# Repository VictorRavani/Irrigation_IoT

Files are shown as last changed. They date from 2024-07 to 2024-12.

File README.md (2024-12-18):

# Irrigation_IoT

Este projeto abrange o desenvolvimento completo de Hardware e Firmware para controle em IoT. Oferece todas as informações e recursos necessários para que qualquer pessoa possa configurar o sistema de forma independente.



# Atualizações a serem feitas v2: 

- Leds dos optocopadores, como os Leds estão em série acaba não havendo corrente sulficinete para acionalos...
- Conversor USB serial CP2102 pode ser removido pois o ESP32-S3 possui interface USB.
- Troca do conector Micro USB para USB tipo C.
- Desing da PCB adaptadada para um case de mercado.
- Substituir botoões por um encoder rotativo.
- Deixar os demais GPIOS disponíveis para uso utilizando conectores KRE. (Obs.: Prever circuitos de proteção com optoacopladores).

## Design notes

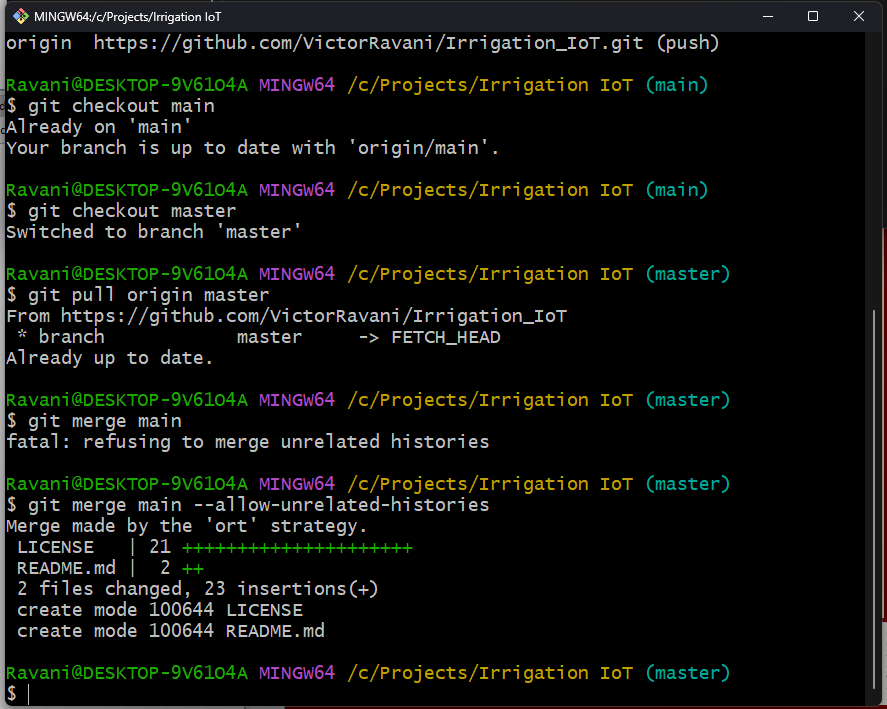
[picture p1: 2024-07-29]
Merge branch master main.png

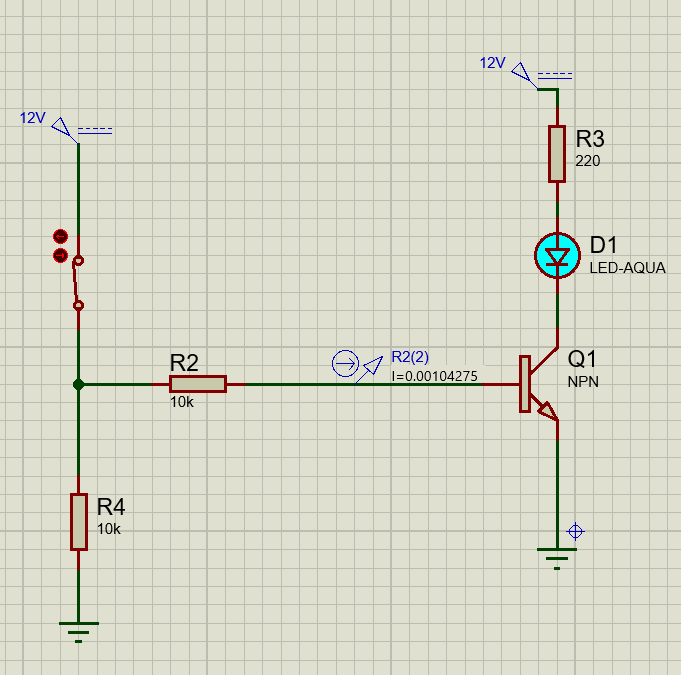
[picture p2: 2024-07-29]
Acionamento Relé.png

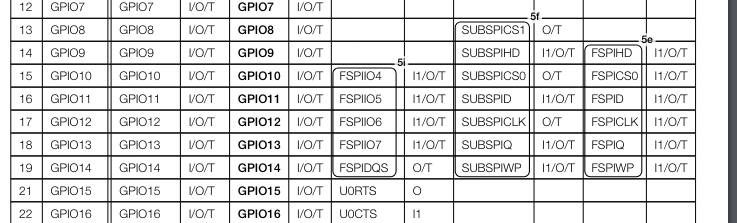
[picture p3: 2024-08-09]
Strappins_ESP32_S3.png

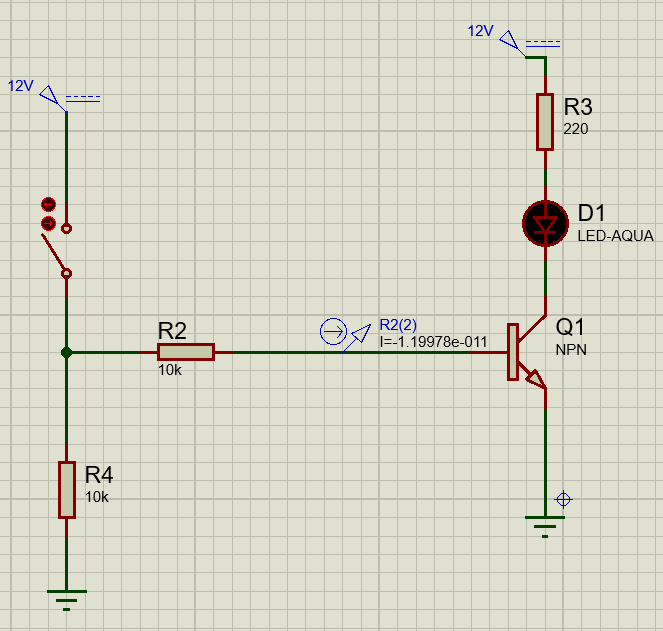
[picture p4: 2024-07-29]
Acionamento Relé aberto.png

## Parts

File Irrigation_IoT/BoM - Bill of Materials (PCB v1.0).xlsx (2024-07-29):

Bill of Materials
Company Name:
Project Name:
Date:
RESISTORS
ID | Qty. | Part Designator | Manufacturer Number | Description
1 |  | R1, R9, R12, R13, R14, R15, R16, R17, |  | Resistor SMD 10K 0805 5%
2 |  | R8, R11 |  | Resistor SMD 2K2 0805 5%
3 |  | R2, R5 |  | Resistor SMD 4K7 0805 5%
4 |  | R3 |  | Resistor SMD 24K 0603 1%
5 |  | R4 |  | Resistor SMD 47K 0603 1%
6 |  | R6, R7, R10 |  | Resistor SMD 220R 0805 5%
CAPACITORS
ID | Qty. | Part Designator | Manufacturer Number | Description
1 | 2 | C1, C7 |  | Capacitor Cerâmico SMD 4,7uF 0805 25V (https://www.eletrodex.net/passivos/capacitores/smd/capacitor-ceramico-smd-0805-x5r-25v)
2 | 9 | C2, C8, C10, C17 |  | Capacitor Cerâmico SMD 10uF 0805 25V (https://www.eletrodex.net/passivos/capacitores/smd/capacitor-ceramico-smd-0805-x5r-25v)
3 | 2 | C3, C5, C6, C9, C11, C12, C13, C14, C15, C16 |  | Capacitor Cerâmico SMD 100nF 0805 50V (https://www.eletrodex.net/passivos/capacitores/smd/capacitor-ceramico-smd-0805-x7r-50v)
INDUCTORS
ID | Qty. | Part Designator | Manufacturer Number | Description
OSCILLATORS
ID | Qty. | Part Designator | Manufacturer Number | Description
TRANSISTORS
ID | Qty. | Part Designator | Manufacturer Number | Description
 |  | Q3, Q4 |  | BC817 NPN (https://www.eletrodex.net/semicondutores/transistores/uso-geral/bc8xxx-transistor-smd)
PROTECTION DEVICES
ID | Qty. | Part Designator | Manufacturer Number | Description
 |  | RV1 (DNP) | MOV-10D431KTR | Varistor 10K AC 275V
DIODES
ID | Qty. | Part Designator | Manufacturer Number | Description
 |  | D1 |  | Diodo Supressor SP0503BAHTG SOT (https://www.acheicomponentes.com.br/circuitos-integrados/kit-5-pecas-diodo-supressor-sp0503bahtg-sot-143-4-smd)
INTREGRATED CIRCUITS
ID | Qty. | Part Designator | Manufacturer Number | Description
 |  | U1, U5 |  | EL817/PC817 ISOLADOR ÓPTICO SMD (https://www.eletrodex.net/semicondutores/opticos/isoladores/el817pc817-isolador-optico)
 |  | IC1 |  | Módulo Esp32-s3 - Esp32-s3-wroom-1 N16r8 (https://produto.mercadolivre.com.br/MLB-3670453135-modulo-esp32-s3-esp32-s3-wroom-1-n16r8-_JM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)
 |  | IC2 |  | Circuito Integrado CP2102-GMR SMD QFN-28 (https://www.acheicomponentes.com.br/circuitos-integrados/smd/circuito-integrado-cp2102-gmr-smd-qfn-28-original-cp2102)
 |  | U1 |  | LM1117DTX-3.3 - 3.3V SMD (https://www.eletrodex.net/semicondutores/ci-s-hibridos/reguladores-lineares/lm1117-regulador-de-tensao-low-dropout)
ELECTROMECHANICS
ID | Qty. | Part Designator | Manufacturer Number | Description
1 | 2 | K3, K4 | MA1RC2 (Metaltex) | Miniature relay AX1RC2 (https://www.eletrodex.net/montagem/reles/miniatura/ma1rc-rele-ultra-miniatura-metaltex)
CONNECTORS
ID | Qty. | Part Designator | Manufacturer Number | Description
1 |  | J1 |  | CONECTOR JACK DC-005 J4, 3T 2,1MM (https://www.eletrodex.net/acessorios/cabos-e-fios/jack/conector-jack-dc-005-j4-3t-2-1mm)
2 |  | J2 |  | CONECTOR USB MICRO-B (https://www.eletrodex.net/conectores/usb/micusb-b5ns-conector-usb-micro-b-para-smd-metaltex)
3 |  | J3, J7 |  | BR7F2-03 (https://www.eletrodex.net/conectores/pci/bornes/borne-plug-metaltex-br7f2-passo-3-81-mm)
4 |  | J8 |  | BR7F2-02 (https://www.eletrodex.net/conectores/pci/bornes/borne-plug-metaltex-br7f2-passo-3-81-mm)
5 |  | J3, J7 |  | BR7MN2-03 (https://www.eletrodex.net/conectores/pci/bornes/br7mn2-borne-receptor-90o-passo-3-81mm-metaltex)
6 |  | J8 |  | BR7MN2-02 (https://www.eletrodex.net/conectores/pci/bornes/br7mn2-borne-receptor-90o-passo-3-81mm-metaltex)
7
8
9
OTHERS
ID | Qty. | Part Designator | Manufacturer Number | Description
 |  | IO0, EN |  | CHAVE TÁCTIL 3X6X4,3 SMD 2 TERMINAIS (https://www.eletrodex.net/montagem/chaves/tactil/chave-tactil-3x6x4-3-smd-2-terminais)
 |  | BT1, BT2, BT3 |  | CHAVE TÁCTIL 6X6x15 4 TERMINAIS PT (https://www.eletrodex.net/montagem/chaves/tactil/chave-tactil-6x6-4-terminais-pt-)

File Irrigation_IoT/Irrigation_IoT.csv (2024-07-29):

Source: | C:\Projects\Irrigation IoT\Irrigation_IoT\Irrigation_IoT.kicad_sch
Date: | 26/06/2024 15:06:21
Tool: | Eeschema 7.0.2
Generator: | C:\Program Files\KiCad\7.0\bin\scripting\plugins/bom_csv_grouped_by_value.py
Component Count: | 73
Collated Components:
Item | Qty | Reference(s) | Value | LibPart | Footprint | Datasheet | DNP | Height | Manufacturer_Name | Manufacturer_Part_Number | Mouser Part Number | Mouser Price/Stock | Sim.Device | Sim.Library | Sim.Name | Sim.Params | Sim.Pins | Tolerância
1 | 3 | BT1, BT2, BT3 | SW_MEC_5G | My_Library_Conectors:Chave_Táctil_Push_Button_SMD_2_Terminais_3x6x4,3_Preta_(KFC-A06) | Button_Switch_THT:SW_PUSH_6mm | http://www.apem.com/int/index.php?controller=attachment&id_attachment=488
2 | 1 | C1 | 4,7uF | Device:C | Capacitor_SMD:C_0805_2012Metric | ~
3 | 4 | C2, C8, C10, C17 | 10uF | Device:C | Capacitor_SMD:C_0805_2012Metric | ~
4 | 10 | C3, C5, C6, C9, C11, C12, C13, C14, C15, C16 | 100nF | Device:C | Capacitor_SMD:C_0805_2012Metric | ~
5 | 1 | C7 | 4.7uF | Device:C | Capacitor_SMD:C_0805_2012Metric | ~
6 | 1 | D1 | SP0503BAHTG | My_library:SP0503BAHTG | My_library_footprint:SP0503BAHTG |  |  | 1.22 | LITTELFUSE | SP0503BAHTG | 576-SP0503BAHTG | https://www.mouser.co.uk/ProductDetail/Littelfuse/SP0503BAHTG?qs=uD%2FdkN7XIa0NTYXwHdELYA%3D%3D
7 | 1 | D2 | SB560 | Diode:SB160 | Diode_THT:D_DO-201AE_P12.70mm_Horizontal | http://www.diodes.com/_files/datasheets/ds23022.pdf
8 | 1 | D3 | SB160 | Diode:SB160 | Diode_THT:D_DO-41_SOD81_P10.16mm_Horizontal | http://www.diodes.com/_files/datasheets/ds23022.pdf
9 | 6 | D4, D5, D6, D7, D8, D9 | 1N4007 | Device:D | My_library_footprint:Diodo_SM_DO-214 | ~ |  |  |  |  |  |  | D |  |  |  | 1=K 2=A
10 | 2 | EN1, IO0 | SW_MEC_5G | My_Library_Conectors:Chave_Táctil_Push_Button_SMD_2_Terminais_3x6x4,3_Preta_(KFC-A06) | My_library_footprint:Chave Táctil Push Button SMD 2 Terminais 3x6x4,3 Preta (KFC-A06) | http://www.apem.com/int/index.php?controller=attachment&id_attachment=488
11 | 1 | F1 | Fuse | Device:Fuse | My_library_footprint:Porta Fusível 5x20 AS-06 | ~
12 | 1 | IC1 | ESP32-S3-WROOM-1-N16R8 | My_Library_MCU:ESP32-S3-WROOM-1-N16R8 | My_MCU_footprint:ESP32S3WROOM1N16R8 | https://www.espressif.com/sites/default/files/documentation/esp32-s3-wroom-1_wroom-1u_datasheet_en.pdf |  | 3.25 | Espressif Systems | ESP32-S3-WROOM-1-N16R8 | 356-ESP32S3WRM1N16R8 | https://www.mouser.co.uk/ProductDetail/Espressif-Systems/ESP32-S3-WROOM-1-N16R8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
13 | 1 | IC2 | CP2102-GM | My_library:CP2102-GM | My_MCU_footprint:CP2102 | https://datasheet.datasheetarchive.com/originals/distributors/Datasheets_SAMA/e8061a629457dcd57bb8c8d46a00fbc0.pdf |  | 1 | Silicon Labs | CP2102-GM | 634-CP2102-GM | https://www.mouser.co.uk/ProductDetail/Silicon-Labs/CP2102-GM?qs=yHCtFi5ROqJvCcyR88R4Pg%3D%3D
14 | 1 | J1 | Barrel_Jack_MountingPin | Connector:Barrel_Jack_MountingPin | Connector_BarrelJack:BarrelJack_GCT_DCJ200-10-A_Horizontal | ~
15 | 1 | J2 | USB_B_Micro | Connector:USB_B_Micro | Connector_USB:USB_Micro-B_Molex-105017-0001 | ~
16 | 2 | J3, J7 | Screw_Terminal_01x03 | Connector:Screw_Terminal_01x03 | My_library_footprint:BR7MN2 - BORNE RECEPTOR 90º PASSO 3,81MM METALTEX | ~
17 | 1 | J4 | I2C Extern | Connector:Conn_01x04_Socket | Connector_PinSocket_2.54mm:PinSocket_1x04_P2.54mm_Horizontal | ~
18 | 1 | J5 | Connector DHT22 | Connector:Conn_01x04_Socket | Connector_PinSocket_2.54mm:PinSocket_1x04_P2.54mm_Horizontal | ~
19 | 1 | J6 | Connector Display | Connector:Conn_01x04_Socket | Connector_PinSocket_2.54mm:PinSocket_1x04_P2.54mm_Vertical | ~
20 | 1 | J8 | Screw_Terminal_01x02 | Connector:Screw_Terminal_01x02 | My_library_footprint:BR7MN2 - 2vias | ~
21 | 2 | J9, J10 | Conn_12V | Connector:Conn_01x02_Pin | Connector_PinHeader_2.54mm:PinHeader_1x02_P2.54mm_Vertical | ~
22 | 2 | K3, K4 | AX1RC2 | Relay:G5Q-1 | My_library_footprint:MA1RC | https://www.omron.com/ecb/products/pdf/en-g5q.pdf
23 | 1 | LED1 | FONT_ON | Device:LED | LED_THT:LED_D3.0mm | ~
24 | 2 | LED2, LED3 | LED_VM | Device:LED | LED_THT:LED_D3.0mm | ~
25 | 4 | Q1, Q2, Q3, Q4 | BC817 | Transistor_BJT:BC817 | Package_TO_SOT_SMD:SOT-23 | https://www.onsemi.com/pub/Collateral/BC818-D.pdf
26 | 3 | R1, R2, R5 | 4K7 | Device:R | Resistor_SMD:R_0805_2012Metric | ~
27 | 1 | R3 | 24K | Device:R | Resistor_SMD:R_0603_1608Metric | ~ |  |  |  |  |  |  |  |  |  |  |  | 1%
28 | 1 | R4 | 47K | Device:R | Resistor_SMD:R_0603_1608Metric | ~ |  |  |  |  |  |  |  |  |  |  |  | 1%
29 | 3 | R6, R7, R10 | 220R | Device:R | Resistor_SMD:R_0805_2012Metric | ~
30 | 2 | R8, R11 | 2K2 | Device:R | Resistor_SMD:R_0805_2012Metric | ~
31 | 7 | R9, R12, R13, R14, R15, R16, R17 | 10K | Device:R | Resistor_SMD:R_0805_2012Metric | ~
32 | 1 | RV1 | Varistor | Device:Varistor | My_library_footprint:Varistor_B72210S0271K101 | ~ |  |  |  |  |  |  | SUBCKT | ${KICAD7_SYMBOL_DIR}/Simulation_SPICE.sp | kicad_builtin_varistor | threshold=1k | 1=A 2=B
33 | 2 | U1, U5 | PC817 | Isolator:PC817 | Package_DIP:DIP-4_W7.62mm_SMDSocket_SmallPads | http://www.soselectronic.cz/a_info/resource/d/pc817.pdf
34 | 1 | U4 | LM1117DT-3.3 | Regulator_Linear:LM1117DT-3.3 | Package_TO_SOT_SMD:SOT-223-3_TabPin2 | http://www.ti.com/lit/ds/symlink/lm1117.pdf

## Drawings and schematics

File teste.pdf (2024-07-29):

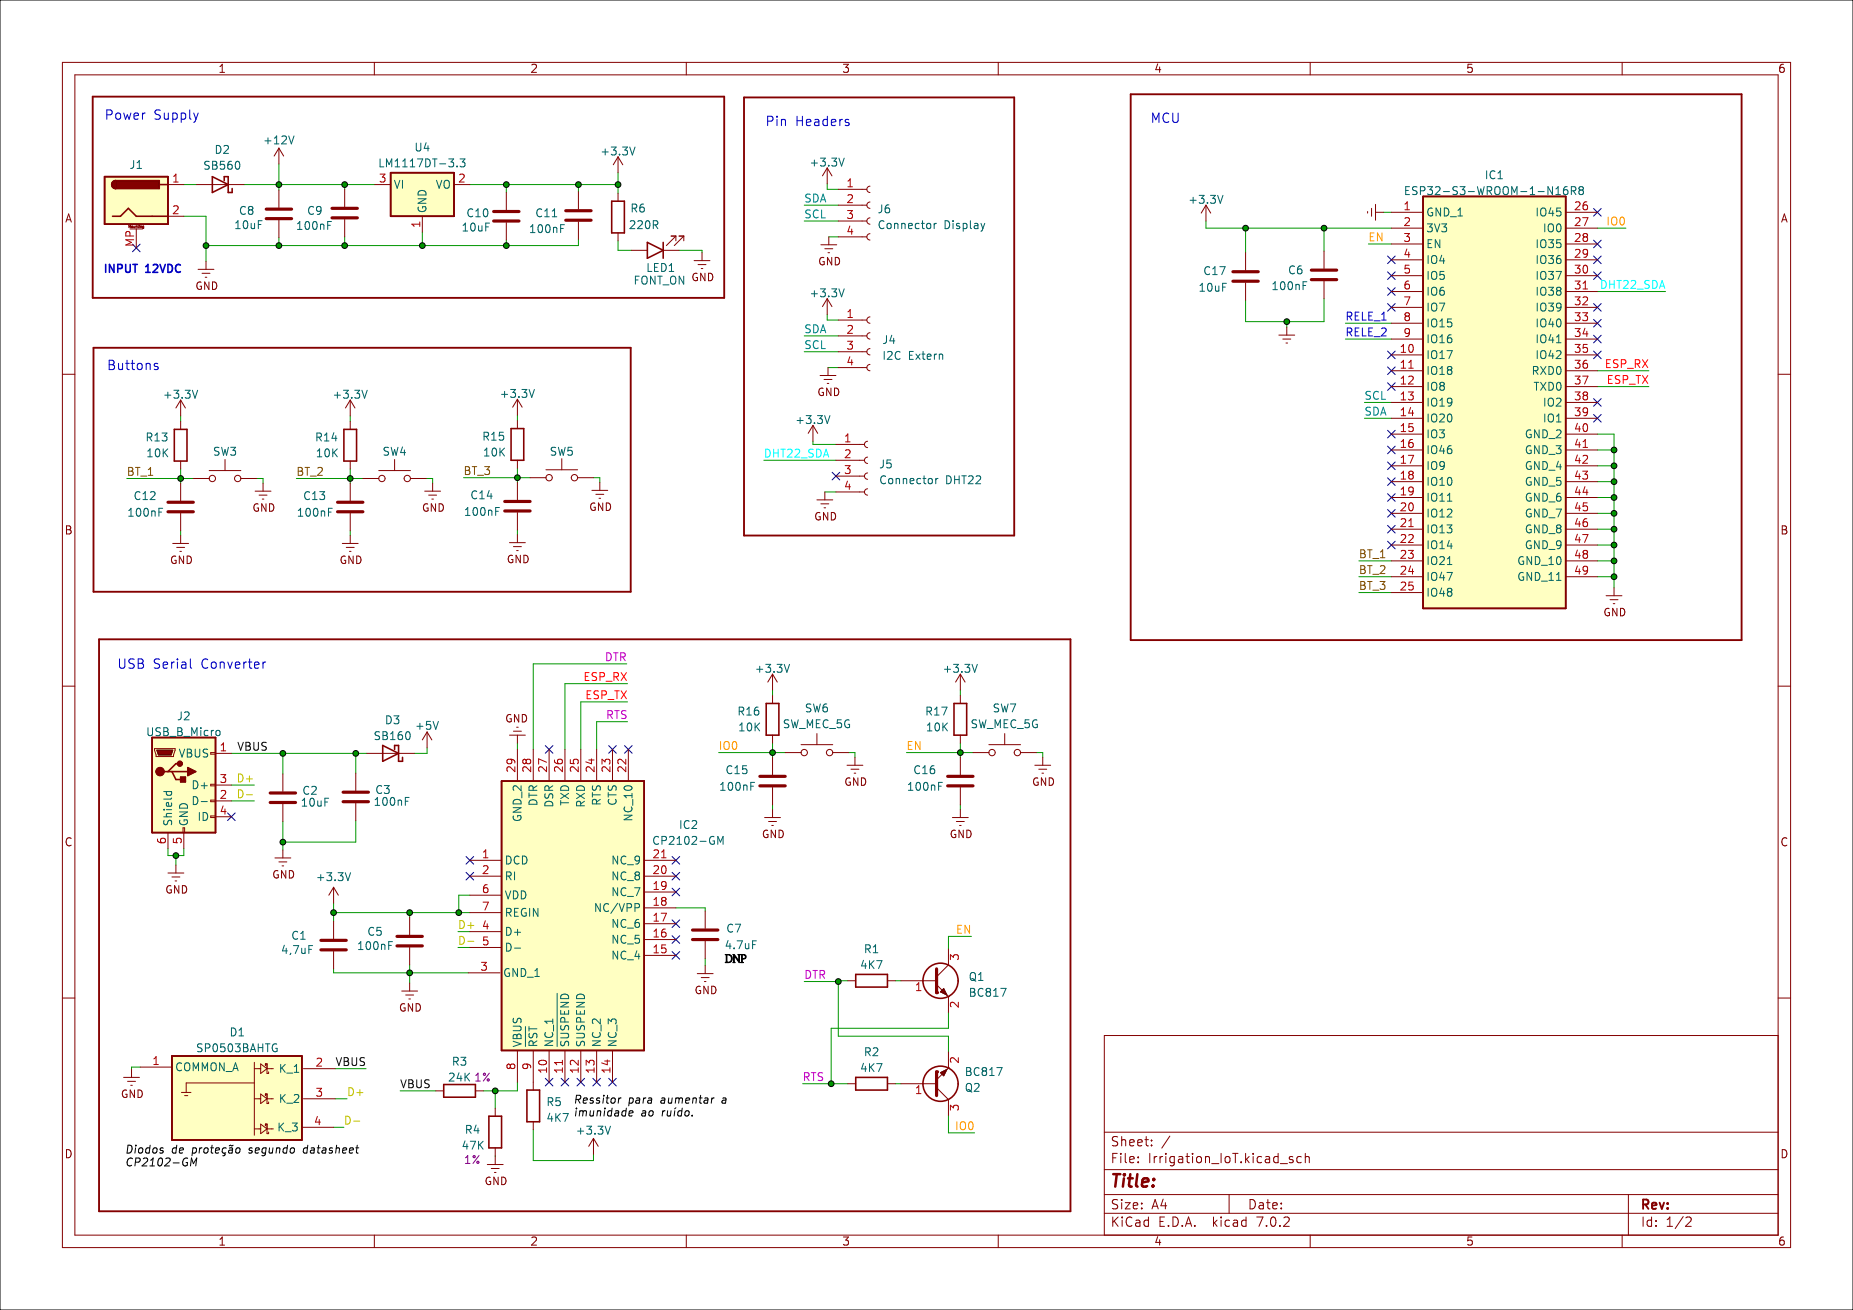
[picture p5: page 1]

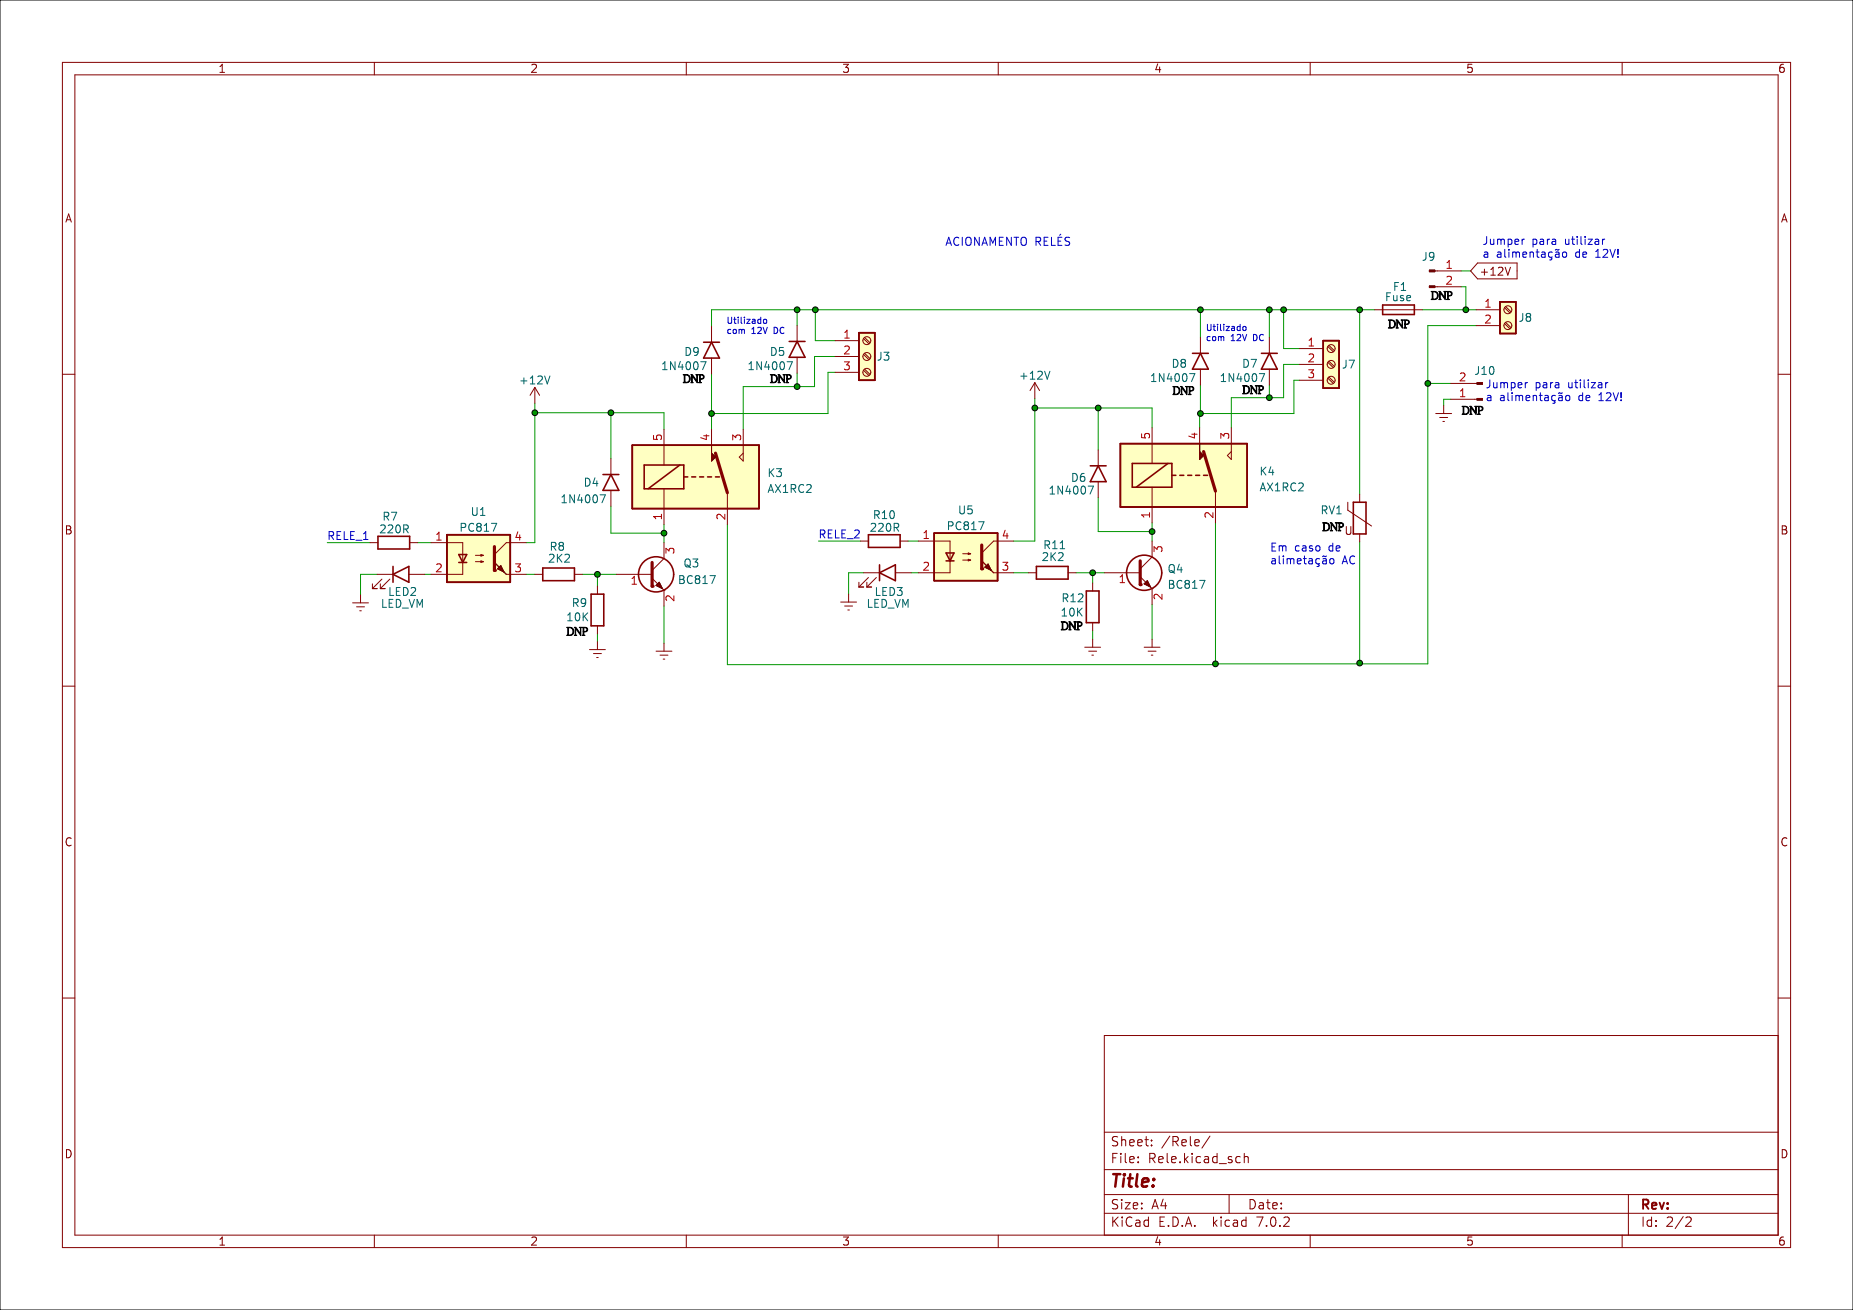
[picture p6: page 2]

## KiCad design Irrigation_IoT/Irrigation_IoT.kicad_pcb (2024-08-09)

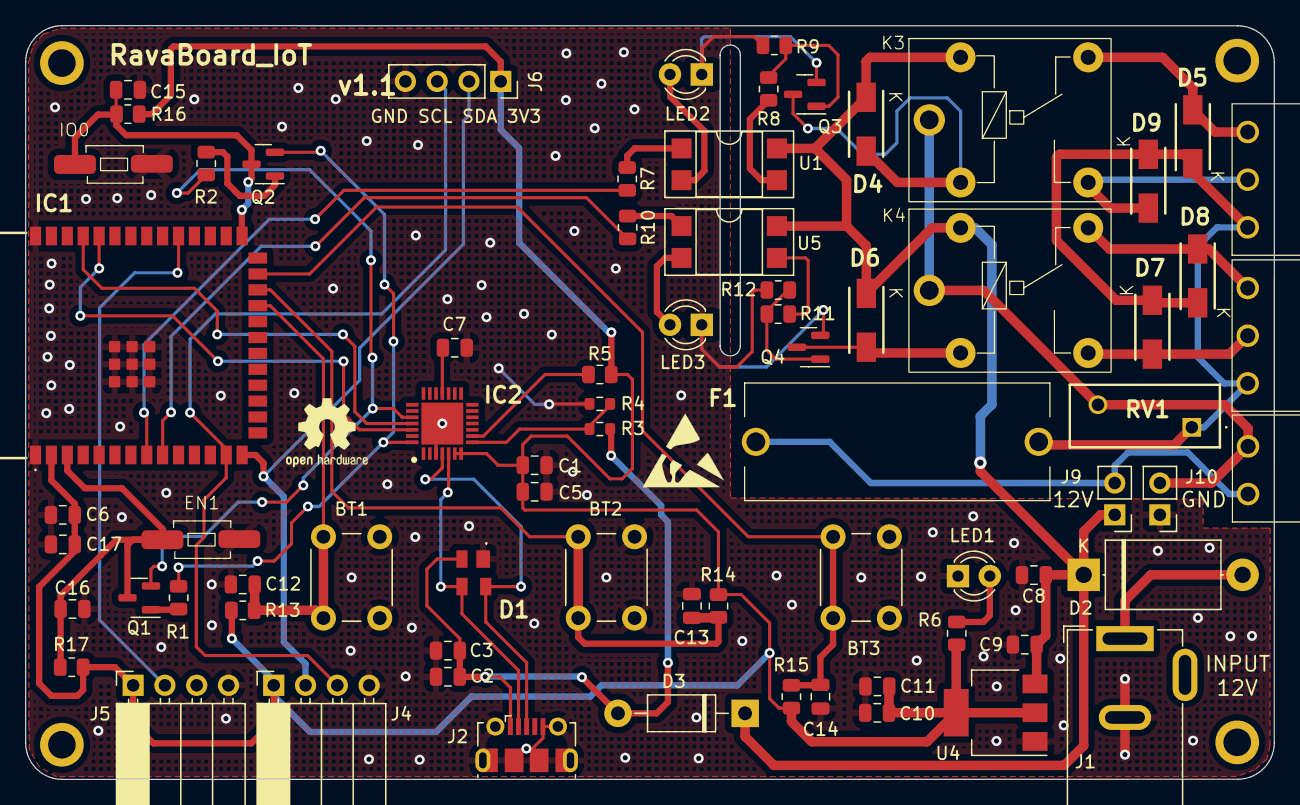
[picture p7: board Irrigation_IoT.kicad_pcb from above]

Board: 2 copper layers, 99.8 x 60.2 mm, 73 parts (0 on the bottom side), 44 nets.

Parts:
BT1, BT2, BT3: SW_MEC_5G; SW_PUSH_6mm
C1: 4,7uF; C_0805_2012Metric
C2, C8, C10, C17: 10uF; C_0805_2012Metric
C3, C5, C6, C9, C11, C12, C13, C14, C15, C16: 100nF; C_0805_2012Metric
C7: 4.7uF; C_0805_2012Metric
D1: SP0503BAHTG
D2: SB560; D_DO-201AE_P12.70mm_Horizontal
D3: SB160; D_DO-41_SOD81_P10.16mm_Horizontal
D4, D5, D6, D7, D8, D9: 1N4007; Diodo_SM_DO-214
EN1: SW_MEC_5G; Chave Táctil Push Button SMD 2 Terminais 3x6x4,3 Preta (KFC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
F1: Fuse; Porta Fusível 5x20 AS-06
IC1: ESP32-S3-WROOM-1-N16R8; ESP32S3WROOM1N16R8
IC2: CP2102-GM; CP2102
IO0: SW_MEC_5G; Chave Táctil Push Button SMD 2 Terminais 3x6x4,3 Preta (KFC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
J1: Barrel_Jack_MountingPin; BarrelJack_GCT_DCJ200-10-A_Horizontal
J2: USB_B_Micro; USB_Micro-B_Molex-105017-0001
J3, J7: Screw_Terminal_01x03; BR7MN2 - BORNE RECEPTOR 90º PASSO 3,81MM METALTEX
J4: I2C Extern; PinSocket_1x04_P2.54mm_Horizontal
J5: Connector DHT22; PinSocket_1x04_P2.54mm_Horizontal
J6: Connector Display; PinSocket_1x04_P2.54mm_Vertical_DISPLAY_OLED
J8: Screw_Terminal_01x02; BR7MN2 - 2vias
J9, J10: Conn_12V; PinHeader_1x02_P2.54mm_Vertical
K3, K4: AX1RC2; MA1RC
LED1: FONT_ON; LED_D3.0mm
LED2, LED3: LED_VM; LED_D3.0mm
Q1, Q2, Q3, Q4: BC817; SOT-23
R1, R2, R5: 4K7; R_0805_2012Metric
R3: 24K; R_0603_1608Metric
R4: 47K; R_0603_1608Metric
R6, R7, R10: 220R; R_0805_2012Metric
R8, R11: 2K2; R_0805_2012Metric
R9, R12, R13, R14, R15, R16, R17: 10K; R_0805_2012Metric
RV1: Varistor; Varistor_B72210S0271K101
U1, U5: PC817; DIP-4_W7.62mm_SMDSocket_SmallPads
U4: LM1117DT-3.3; SOT-223-3_TabPin2

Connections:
+3.3V: C1.1, C5.1, C6.1, C10.1, C11.1, C17.1, IC1.2 (3V3), IC2.6 (VDD), IC2.7 (REGIN), J4.1, J5.1, J6.1, R5.2, R6.1, R13.1, R14.1, R15.1, R16.1, R17.1, U4.2 (VO)
+12V: C8.1, C9.1, D2.1 (K), D3.1 (K), D4.1 (K), D6.1 (K), J9.1, K3.5, K4.5, U1.4, U4.3 (VI), U5.4
/BT_1: BT1.1, C12.1, IC1.23 (IO21), R13.2
/BT_2: BT2.1, C13.1, IC1.24 (IO47), R14.2
/BT_3: BT3.1, C14.1, IC1.25 (IO48), R15.2
/D+: D1.4 (K_3), IC2.4 (D+), J2.3 (D+)
/D-: D1.3 (K_2), IC2.5 (D-), J2.2 (D-)
/DHT22_SDA: IC1.31 (IO38), J5.2
/DTR: IC2.28 (DTR), Q2.2 (E), R1.1
/EN: C16.1, EN1.1, IC1.3 (EN), Q1.3 (C), R17.2
/ESP_RX: IC1.36 (RXD0), IC2.26 (TXD)
/ESP_TX: IC1.37 (TXD0), IC2.25 (RXD)
/IO0: C15.1, IC1.27 (IO0), IO0.1, Q2.3 (C), R16.2
/RELE_1: IC1.8 (IO15), R7.2
/RELE_2: IC1.9 (IO16), R10.2
/RTS: IC2.24 (RTS), Q1.2 (E), R2.1
/SCL: IC1.13 (IO19), J4.3, J6.3
/SDA: IC1.14 (IO20), J4.2, J6.2
/VBUS: C2.1, C3.1, D1.2 (K_1), D3.2 (A), J2.1 (VBUS), R3.1
Earth: BT1.2, BT2.2, BT3.2, C1.2, C2.2, C3.2, C5.2, C6.2, C7.2, C8.2, C9.2, C10.2, C11.2, C12.2, C13.2, C14.2, C15.2, C16.2, C17.2, D1.1 (COMMON_A), EN1.2, IC1.1 (GND_1), IC1.40 (GND_2), IC1.41 (GND_3), IC1.42 (GND_4), IC1.43 (GND_5), IC1.44 (GND_6), IC1.45 (GND_7), IC1.46 (GND_8), IC1.47 (GND_9), IC1.48 (GND_10), IC1.49 (GND_11), IC2.3 (GND_1), IC2.29 (GND_2), IO0.2, J1.2, J2.5 (GND), J2.6 (Shield), J4.4, J5.4, J6.4, J10.1, LED1.1 (K), LED2.1 (K), LED3.1 (K), Q3.2 (E), Q4.2 (E), R4.1, R9.2, R12.2, U4.1 (GND)
unnamed: D2.2 (A), J1.1
unnamed: D4.2 (A), K3.1, Q3.3 (C)
unnamed: D5.2 (A), J3.2, K3.3
unnamed: D5.1 (K), D7.1 (K), D8.1 (K), D9.1 (K), F1.1, J3.1, J7.1, RV1.1
unnamed: D6.2 (A), K4.1, Q4.3 (C)
unnamed: D7.2 (A), J7.2, K4.3
unnamed: D8.2 (A), J7.3, K4.4
unnamed: D9.2 (A), J3.3, K3.4
unnamed: C7.1, IC2.18 (NC/VPP)
unnamed: IC2.8 (VBUS), R3.2, R4.2
unnamed: IC2.9 (~RST), R5.1
unnamed: F1.2, J8.1, J9.2
unnamed: J8.2, J10.2, K3.2, K4.2, RV1.2
unnamed: LED1.2 (A), R6.2
unnamed: LED2.2 (A), U1.2
unnamed: LED3.2 (A), U5.2
unnamed: Q1.1 (B), R1.2
unnamed: Q2.1 (B), R2.2
unnamed: Q3.1 (B), R8.1
unnamed: Q4.1 (B), R11.1, R12.1
unnamed: R7.1, U1.1
unnamed: R8.2, R9.1, U1.3
unnamed: R10.1, U5.1
unnamed: R11.2, U5.3

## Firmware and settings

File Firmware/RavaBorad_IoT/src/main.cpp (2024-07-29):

#include <Arduino.h>

#include <SPI.h>
#include <Wire.h>
#include <Adafruit_GFX.h>
#include <Adafruit_SSD1306.h>

#define SCREEN_WIDTH 128
#define SCREEN_HEIGHT 64
 
#define OLED_RESET -1

Adafruit_SSD1306 display(SCREEN_WIDTH, SCREEN_HEIGHT, &Wire, OLED_RESET);

void setup() {
  Serial.begin(115200);
  Wire.setPins(20, 19);
  Wire.begin();

  display.begin(SSD1306_SWITCHCAPVCC, 0x3C);
  display.clearDisplay();

    display.setTextSize(2);
  display.setTextColor(WHITE);
  display.setCursor(0,10);
  display.print("TESTE");
  display.setCursor(0,30);
  display.print("PCB");
  display.display();

  delay(5000);

}

void loop() {

  Serial.println("Teste Serial");
  delay(1000);
}

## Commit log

2024-07-29 Frist commit
    [1.xlsx, BoM - Bill of Materials (PCB v1.0).xlsx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]
2024-07-29 Inclusão do step
    [Irrigation_IoT.kicad_pcb]
2024-08-09 atualização de arquivos
    [Irrigation_IoT.kicad_pcb, Irrigation_IoT.kicad_sch, Rele.kicad_sch]
